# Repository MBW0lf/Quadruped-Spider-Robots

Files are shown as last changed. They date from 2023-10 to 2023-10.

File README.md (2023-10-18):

# Quadruped-Spider-Robots

<!-- TABLE OF CONTENTS -->
<details>
  <summary>Table of Contents</summary>
  <ol>
    <li><a href="#about-the-project">About The Project</a></li>
    <li><a href="#components">Components</a></li>
    <li><a href="#results">Results</a></li>
    <li><a href="#contact">Contact</a></li>
  </ol>
</details>

<!-- ABOUT THE PROJECT -->
# About The Project

In this project, we initially designed the robot model, manufactured the robot components using a 3D printer, and assembled them. Subsequently, we programmed the robot's movements. Finally, employing image processing, we detected obstacles and reached the destination using existing algorithms.

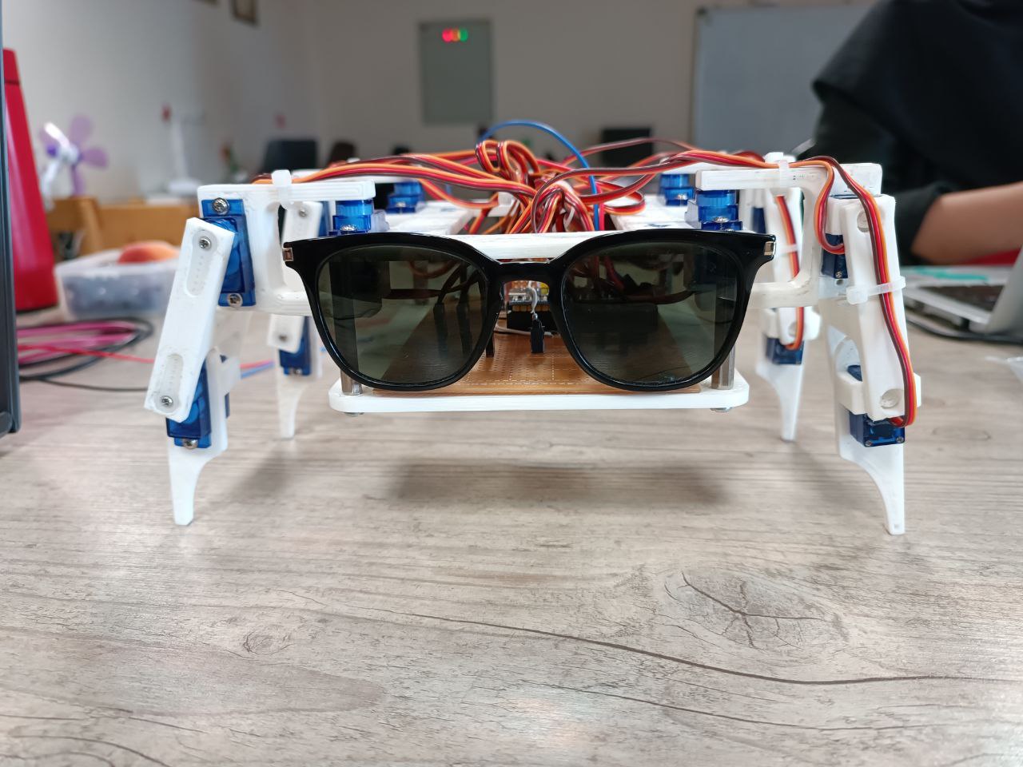
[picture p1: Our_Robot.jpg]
 

<p align="right">(<a href="#top">back to top</a>)</p>

# Components
 * Main proccessor: [STM32F103C8T6 (ARM Cortex-M3)](https://amjadkala.com/product/stm32f103c8t6-board/)
 * Motor: [Servo Motor SG90](https://eshop.eca.ir/%D8%B3%D8%B1%D9%88%D9%88%D9%85%D9%88%D8%AA%D9%88%D8%B1/2551-%D8%B3%D8%B1%D9%88-%D9%85%D9%88%D8%AA%D9%88%D8%B1-t-pro-mini-servo-sg90-9g-servo.htm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)
 * Camera: [ESP32-CAM](https://eshop.eca.ir/%D9%85%D8%A7%DA%98%D9%88%D9%84-%D9%BE%D8%B1%D8%AF%D8%A7%D8%B2%D8%B4-%D8%AA%D8%B5%D9%88%DB%8C%D8%B1-%D9%88-%D8%AF%D9%88%D8%B1%D8%A8%DB%8C%D9%86/1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) 
 * Source Voltage: [HJS-480-0-24](https://bir-robotic.ir/product/%D9%85%D9%86%D8%A8%D8%B9-%D8%AA%D8%BA%D8%B0%DB%8C%D9%87-%D8%B3%D9%88%D8%A6%DB%8C%DA%86%DB%8C%D9%86%DA%AF-24-%D9%88%D9%84%D8%AA-20-%D8%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)
 
<p align="right">(<a href="#top">back to top</a>)</p>

<!-- PARTS -->
# Results

**Robot Without Motors**

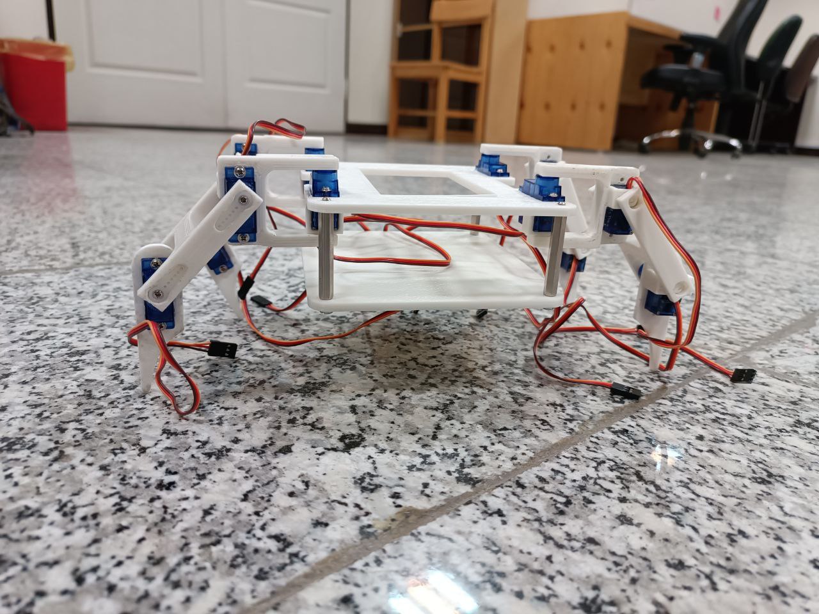
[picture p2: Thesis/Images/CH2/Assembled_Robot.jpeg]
 

**Robot From The Front**

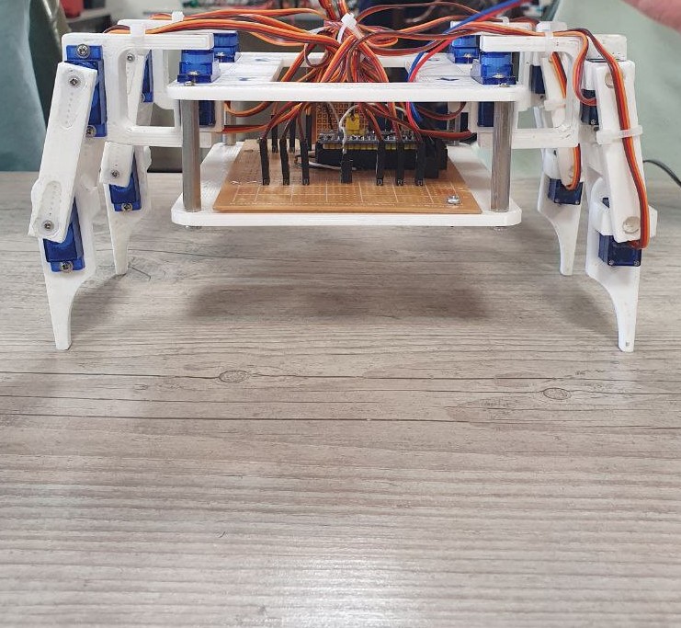
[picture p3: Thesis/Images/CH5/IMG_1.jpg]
 

**Robot From The Top**

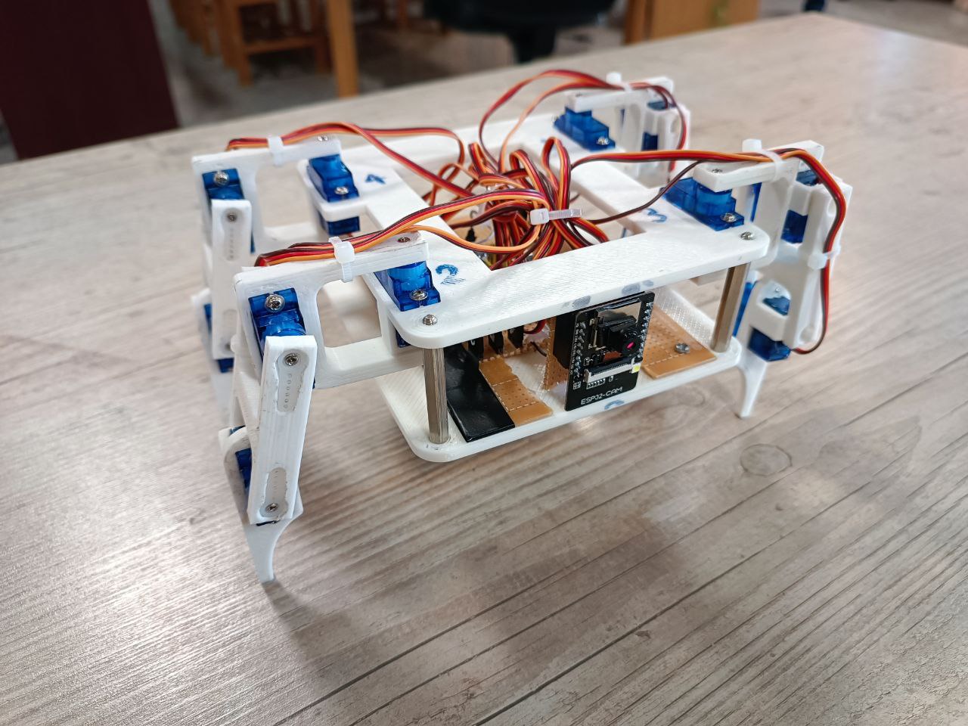
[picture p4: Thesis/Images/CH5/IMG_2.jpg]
 

**Final Verion In SolidWorks**

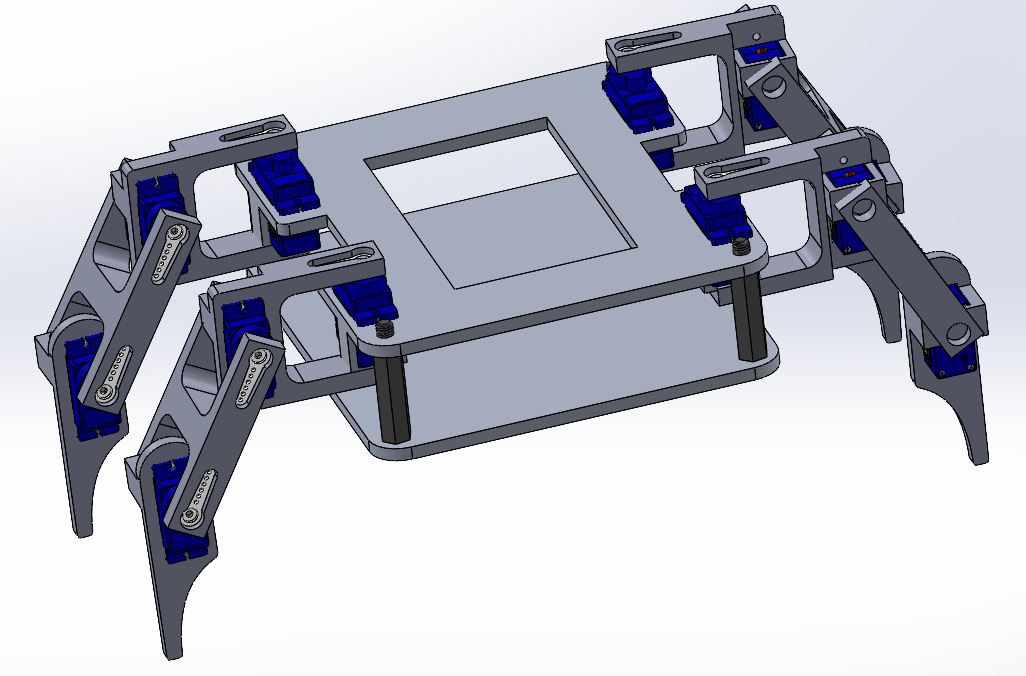
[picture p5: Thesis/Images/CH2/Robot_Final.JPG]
 

<p align="right">(<a href="#top">back to top</a>)</p>

<!-- CONTACT -->
# Contact

Mohammad Barabadi - [@MBW0lf](https://github.com/MBW0lf) - reyneh.100.mb@gmail.com

Sajad Ghadiri - [@Sajad-Ghadiri](https://github.com/Sajad-Ghadiri) - cjanthony.romeo@gmail.com

Project Links: [https://github.com/MBW0lf/Quadruped-Spider-Robots](https://github.com/MBW0lf/Quadruped-Spider-Robots)

<p align="right">(<a href="#top">back to top</a>)</p>

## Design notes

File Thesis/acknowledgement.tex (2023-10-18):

%%%%%%%%%%%%%%%%%%%%%%%%%%%%%%%%%%%%
\newpage\thispagestyle{empty}
% سپاس‌گزاری
\textbf{تقدیر و تشکر}
\\[2cm]

تشکر قلبی و لسانی خود را از استاد عالی قدر جناب دکتر محمد اعظم خسروی که زحمت راهنمایی این پایان نامه را عهده دار گردیدند و در تمامی مراحل انجام رساله از راهنمایی‌های مدبّرانه ایشان استفاده نمودم ابراز می‌دارم و توفیقات روز افزون ایشان را توأم با صحت و سعادت خواستارم.

از جناب دكتر مسعود شفيعي كه زحمت داوري و تصحيح اين پايان نامه را به عهده داشتند كمال سپاس را دارم.

از همگروهي عزيز مهندس سجاد قدیری كه همواره يار و ياوري صبور بود كمال تشكر را دارم.
 
و در پایان از تمامی عزیزانی که در طول انجام این پروژه مرا یاری کرده‌اند کمال تشکر و قدردانی را ابراز می‌نمایم.

% با استفاده از دستور زیر، امضای شما، به طور خودکار، درج می‌شود.
%\signature

%%%%%%%%%%%%%%%%%%%%%%%%%%%%%%%%%%%%%%%%%
%%%%%%%%%%%%%%%%%%%%%%%%%%%%%%%%%کدهای زیر را تغییر ندهید.
\newpage\clearpage

\pagestyle{style2}

\vspace*{-1cm}
\section*{\centering چکیده}
%\addcontentsline{toc}{chapter}{چکیده}
\vspace*{.5cm}
\ffa-abstract
\vspace*{2cm}

{\noindent\large\textbf{واژه‌های کلیدی:}}\par
\vspace*{.5cm}
\fkeywords

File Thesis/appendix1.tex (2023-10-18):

\chapter*{‌پیوست}
\markboth{پیوست}{}
\addcontentsline{toc}{chapter}{پیوست}
کد کامل شامل 1300 خط است که به چندین فایل تقسیم کردیم که ما داخل فایل \lr{Main} تغییرات را ایجاد می‌کنیم و در اینجا توابع و دستورات مهم را آوردیم.

    \begin{figure}[!h]
	\centering
	
	
	\vspace{0.5cm}
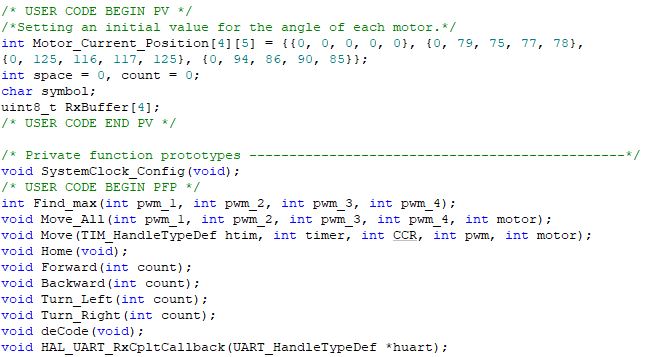
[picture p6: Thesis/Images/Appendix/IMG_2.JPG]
	
	\end{figure}
	
	\begin{figure}[!h]
	\centering
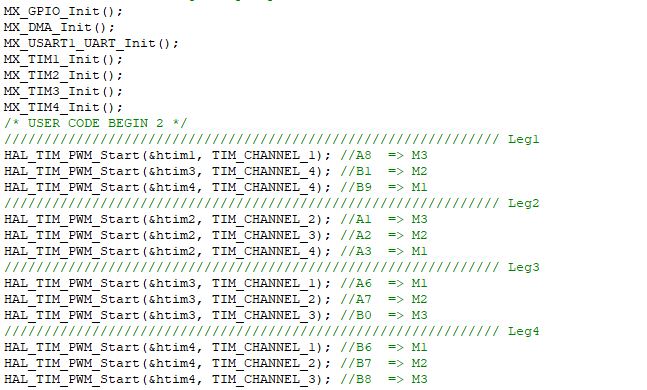
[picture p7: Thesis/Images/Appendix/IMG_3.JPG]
	
		
	\vspace{0.5cm}
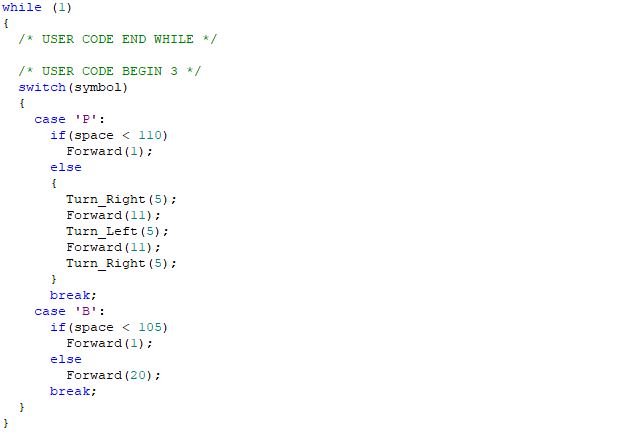
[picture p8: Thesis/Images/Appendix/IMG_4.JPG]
	
	\end{figure}
	
	\begin{figure}[!h]
	\centering
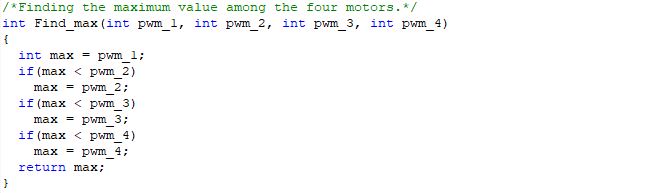
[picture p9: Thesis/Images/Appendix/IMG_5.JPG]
	
		
	\vspace{0.5cm}
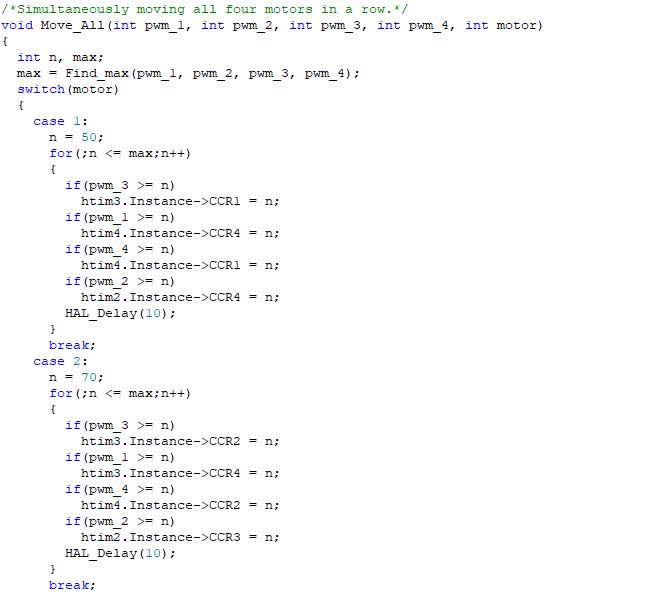
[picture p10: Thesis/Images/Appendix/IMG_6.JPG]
	
	\end{figure}
	
	\begin{figure}[!h]
	\centering
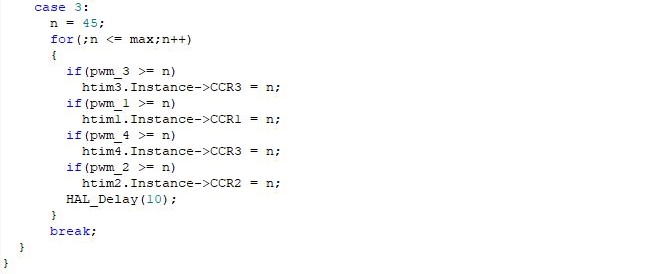
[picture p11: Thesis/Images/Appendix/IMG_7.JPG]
	
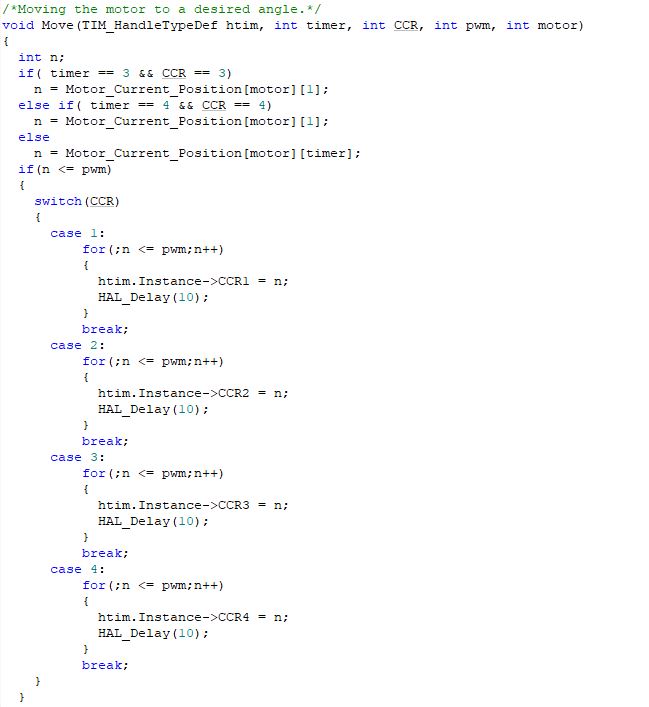
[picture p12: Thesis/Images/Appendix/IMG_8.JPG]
	
	\end{figure}
	
	\begin{figure}[!h]
	\centering
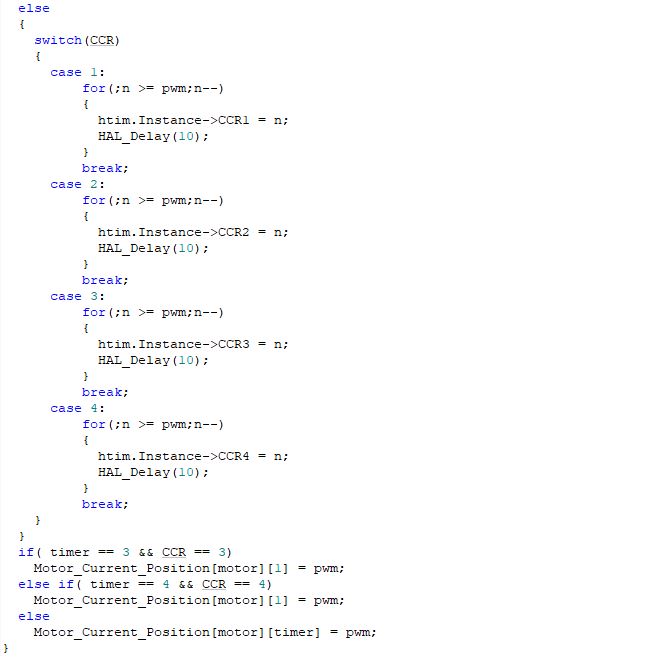
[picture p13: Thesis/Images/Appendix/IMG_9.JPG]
	
			
	\vspace{0.5cm}
	
	\end{figure}
	
	\begin{figure}[!h]
	\centering
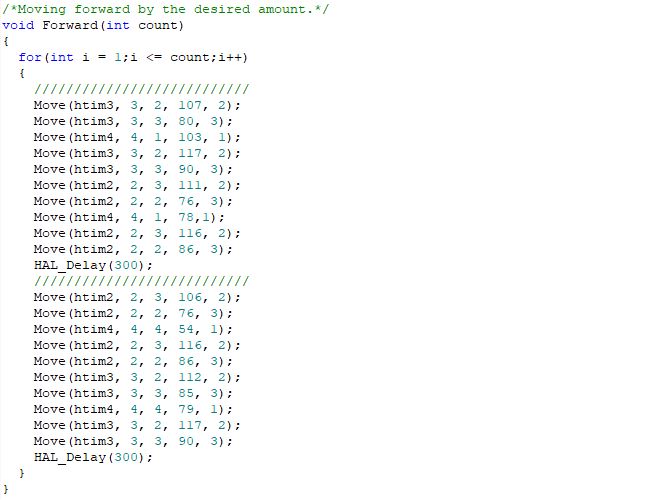
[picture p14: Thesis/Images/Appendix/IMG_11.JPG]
	
		
	\vspace{0.5cm}
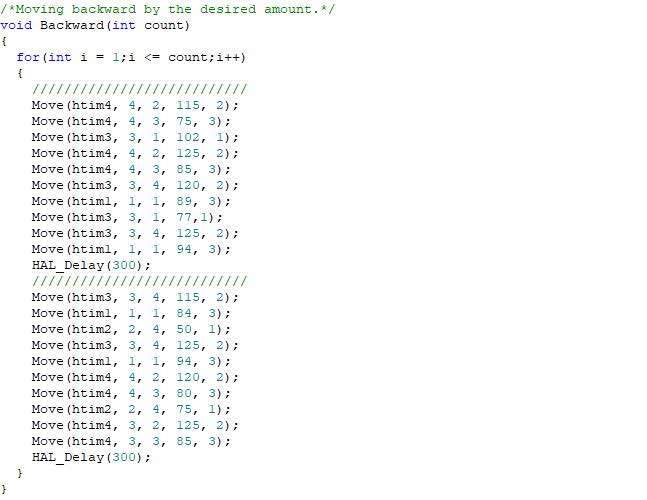
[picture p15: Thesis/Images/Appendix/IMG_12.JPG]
	
	\end{figure}
	
	\begin{figure}[!h]
	\centering
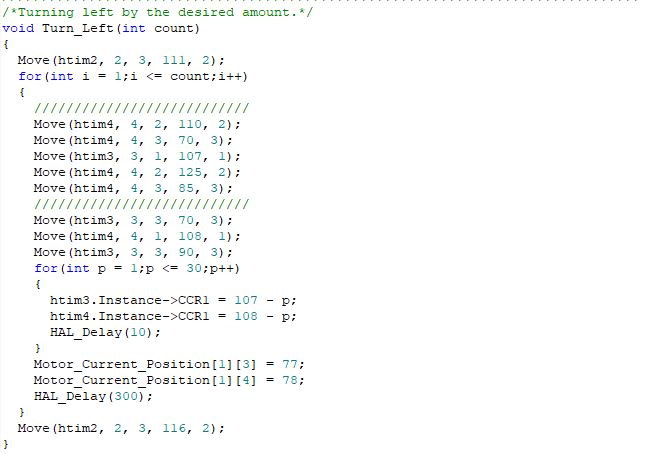
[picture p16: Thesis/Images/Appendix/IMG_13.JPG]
	
	
	\vspace{0.5cm}
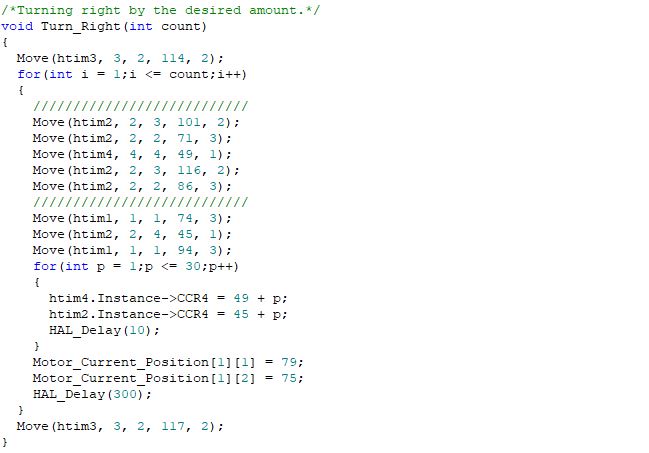
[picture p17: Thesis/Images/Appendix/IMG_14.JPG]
	
	\end{figure}	
	
	\begin{figure}[!h]
	\centering
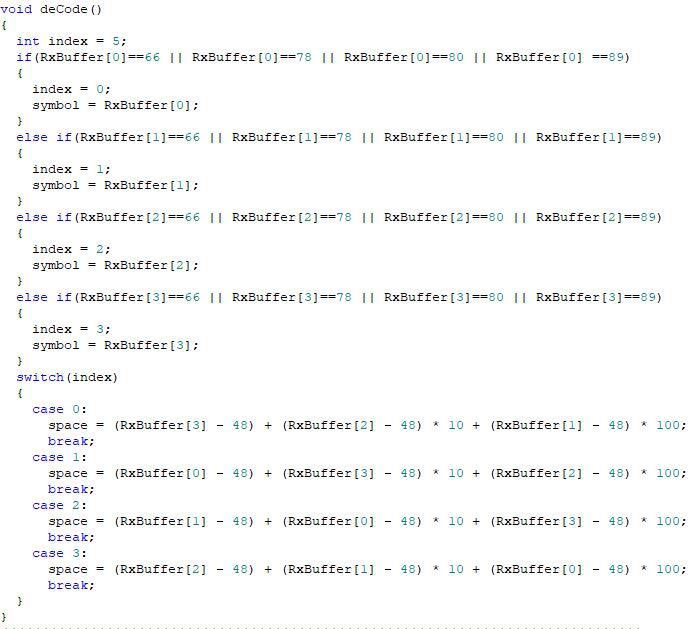
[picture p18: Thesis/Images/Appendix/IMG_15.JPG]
	
	
	\vspace{0.5cm}
	
	\end{figure}

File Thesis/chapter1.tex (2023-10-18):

\chapter{مقدمه}

\section{مقدمه}
با پیشرفت‌های چشمگیر در فناوری و مهندسی در چند دهه اخیر، یک انقلاب قابل توجه در زمینه رباتیک رخ داده است. رباتیک به عنوان یک زمینه چندجانبه و قابل اجرا، شامل تحقیقات و توسعه در طراحی، ساخت، کنترل و بهینه‌سازی ربات‌ها می‌شود. با ترکیب فناوری‌های مختلف از جمله مکانیک، الکترونیک، نرم‌افزار و هوش مصنوعی، ربات‌ها به وجود می‌آیند که قادر به انجام طیف گسترده‌ای از وظایف هستند؛ از فعالیت‌های صنعتی و خدماتی تا کارهای پزشکی، کشاورزی و حتی بررسی فضا.

امروزه از علم رباتیک برای ایجاد دستگاه‌های خودکار به کمک هوش مصنوعی که بتوانند وظایفی مشابه انسان‌ها را با دقت و کارایی بیشتری انجام دهند، استفاده می‌شود. برای رسیدن به این هدف، محققان و مهندسان در زمینه رباتیک تلاش می‌کنند تا مکانیسم‌های پیچیده‌تری برای حرکت، احساس، تصمیم‌گیری و تعامل با محیط ایجاد کنند.

\section[ربات و انواع آن]{ربات و انواع آن\cite{Digiato}}
ربات یک ماشین است (به‌خصوص ماشینی که توسط کامپیوتر قابل برنامه‌نویسی باشد) که می‌تواند مجموعه کارهای پیچیده‌ای را به‌صورت خودکار انجام دهد.ربات‌ها ممکن است توسط یک دستگاه کنترل خارجی، کنترل شوند یا این‌که دستگاه کنترلی در داخل آن‌ها قرار بگیرد. ربات‌ها ممکن است به‌گونه‌ای ساخته شوند که ظاهری شبیه به انسان داشته باشند اما بیشتر ربات‌ها، ماشین‌هایی هستند که برای انجام کاری ساخته می‌شوند و ظاهر آن‌ها اهمیتی ندارد. 

ربات‌ها ممکن است خودران\LTRfootnote{Autonomous} یا نیمه خودران\LTRfootnote{Semi-Autonomous} باشند و انواع مختلفی دارند؛ از قبیل ربات‌های انسان‌نما، مانند ربات
\lr{ASIMO}
 شرکت هوندا و ربات پینگ‌پونگ‌باز شرکت 
\lr{TOSY}
، ربات‌های صنعتی، ربات‌های جراحی پزشکی، ربات‌های کوچک که از هوش جمعی بهره می‌برند، پهباد هایی مانند هواپیمای بدون سرنشین
\lr{Predator MQ-1}
که توسط نیروی هوایی ایالات‌ متحده مورداستفاده قرار می‌گیرد و حتی ربات‌های میکروسکوپی(نانو ربات‌ها)\cite{Digiato}. ربات‌ها ممکن است با تقلید از ظاهر موجودات زنده و یا شبیه‌سازی حرکات آن‌ها، حس هوشمند بودن و یا توانایی فکر کردن را به انسان القا کنند. انتظار می‌رود تا در دهه آتی، اشیا خودران گسترش چشمگیری پیدا کنند. از ارکان اصلی این گسترش می‌توان به ربات‌های خانگی و اتومبیل‌های خودران اشاره کرد.
\newpage
ربات‌ها انواع گوناگونی دارند و هر نوع برای کاربردهای خاصی طراحی شده است. در ادامه به بررسی برخی از انواع مختلف ربات‌ها و ویژگی‌های منحصربه‌فرد آنها می‌پردازیم:

\vspace{0.5cm}
\textbf{1- ربات‌های صنعتی}:
  امروزه پیچیدگی‌های فرایند تولید در صنایع مختلف، افزایش حجم کار و البته رقابتی بودن بازار، منجر به جایگزینی ربات صنعتی با نیروی انسانی شده است. واقعیت این است که در نظر گرفتن حفظ سلامت نیروی کار، جلوگیری از بروز خطا حین فرایند تولید و افزایش سرعت ایجاب می‌کند که از ربات ها به ویژه ربات صنعتی به عنوان بهترین جایگزین برای نیروی انسانی استفاده شود.
  
  ربات صنعتی در واقع یک سیستم اتوماتیک است که برای انجام مراحل مختلف فرآیند تولید محصول در انواع صنایع استفاده می‌شود. اغلب این ربات‌ها به طور کامل قابل برنامه‌ریزی هستند و سرعت و دقت انجام کار را به طور چشم‌گیری افزایش می‌دهند. ربات های صنعتی در ابعاد مختلف تولید می‌شوند؛ از نانو و میکرو گرفته تا ابعاد بزرگتر و کارخانه‌ای، قابلیت اضافه شدن به خط تولید را دارند.
    \begin{figure}[!h]
  	\vspace{0.2cm}
  	\centering
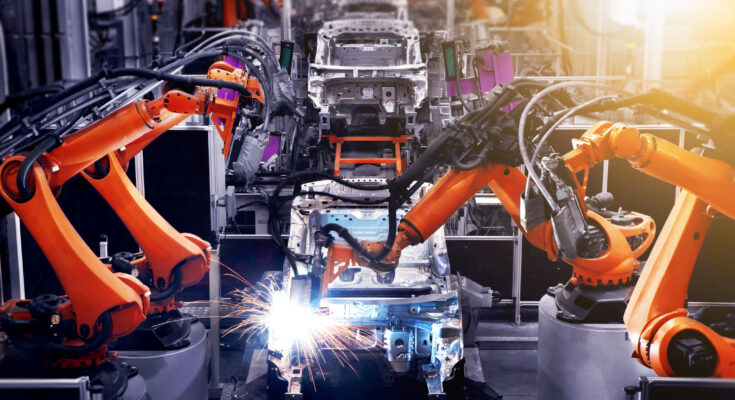
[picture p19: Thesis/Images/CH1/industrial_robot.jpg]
  	
  	\caption{نمونه ربات صنعتی}
  	\label{ربات سنعتی}
    \end{figure}

\textbf{2- ربات‌های خدماتی}:
  ربات‌های خدماتی، نوعی سیستم هوش مصنوعی، به عنوان یک پیشرفت فناوری مهم در سال‌های اخیر ظهور کرده‌اند. این ربات‌ها برای انجام وظایف و عملکردهای متنوع در محیط‌های مختلف طراحی و برنامه‌ریزی شده‌اند تا زندگی انسان‌ها را بهبود بخشند و خدمات گوناگونی را فراهم آورند. برخلاف ربات‌های صنعتی که عمدتاً در کارخانه‌ها عمل می‌کنند، ربات‌های خدماتی برای تعامل مستقیم با انسان‌ها طراحی شده‌اند و در محیط‌های مختلفی نظیر خانه‌ها، مراکز درمانی، بخش هتل‌ها، فضاهای عمومی و غیره عمل می‌کنند.
\newpage
\begin{itemize}
	\item ربات‌های خانگی: این ربات‌ها در کمک به کارهای خانگی نظیر جارو‌کردن، کوتاه کردن چمن و تمیز کردن استفاده می‌شوند.
    \begin{figure}[!h]
	\vspace{0.2cm}
	\centering
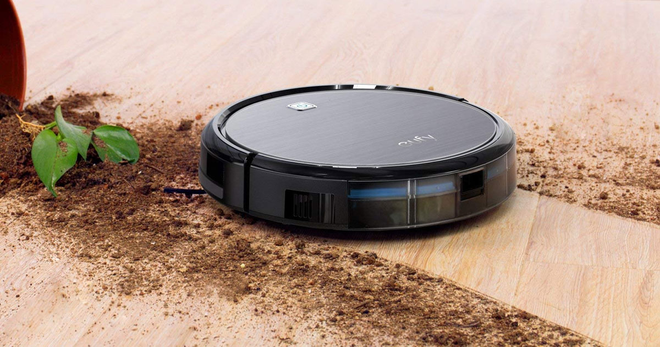
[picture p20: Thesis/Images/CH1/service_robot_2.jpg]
	
	\caption{نمونه‌ای از ربات خانگی}
	\label{ربات خانگی}
	\end{figure}
	
	\item ربات‌های پزشکی: در محیط‌های درمانی برای انجام عملیات‌های جراحی، مراقبت از بیماران و بازسازی استفاده می‌شوند.
    \begin{figure}[!h]
	\vspace{0.2cm}
	\centering
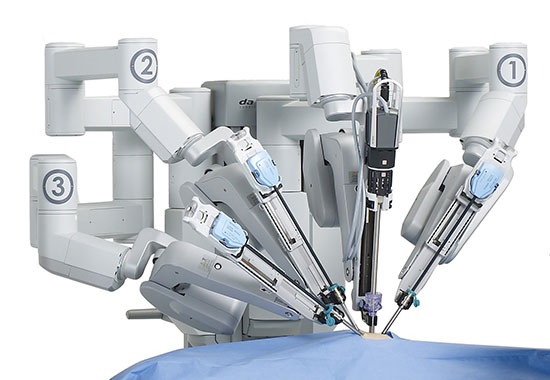
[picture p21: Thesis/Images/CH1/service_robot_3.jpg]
	
	\caption{ربات جراح}
	\label{ربات جراح}
	\end{figure}

	\item ربات‌های سرگرمی: برای اهداف سرگرمی طراحی شده‌اند، از اسباب‌بازی‌ها و همراهان رباتی تا کاربردهای سرگرمی دیگر.
	
    \begin{figure}[!h]
	\vspace{0.2cm}
	\centering
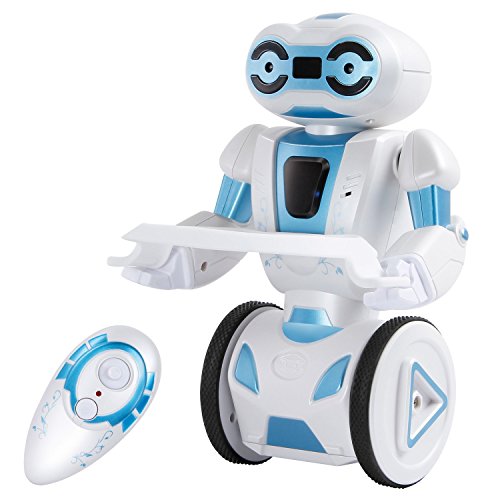
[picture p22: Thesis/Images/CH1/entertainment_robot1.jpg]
	
	\caption{یک نمونه ربات سرگرمی}
	\label{ربات سرگرمی}
	\end{figure}

\end{itemize}	
 
\textbf{3- وسایل خودران}:
  ربات‌های خودران می‌توانند وظایف خود را به‌صورت کاملاً خودکار و بدون نیاز به نظارت و کنترل انسان انجام دهند. این ربات‌ها معمولاً برای فعالیت در محیط‌های باز که فعالیت کردن در آن‌ها نیازی به نظارت انسان ندارد، طراحی شده‌اند. چنین ربات‌هایی طراحی منحصربه‌فردی دارند؛ زیرا با برخورداری از سنسورهای مختلف می‌توانند محیط اطراف خود را به‌خوبی درک کنند و سپس با بهره‌مندی با آن دسته از تجهیزات خود که برای تصمیم‌گیری به ربات کمک می‌کنند (معمولاً کامپیوترهای خاصی این کار را انجام می‌دهند)، بر اساس داده‌های در اختیار خود و همچنین مأموریتی که به آن‌ها محول شده است، تصمیم مناسب را برای انجام کار بعدی به بهترین شکل ممکن می‌گیرند.
    \begin{figure}[!h]
	\vspace{0.2cm}
	\centering
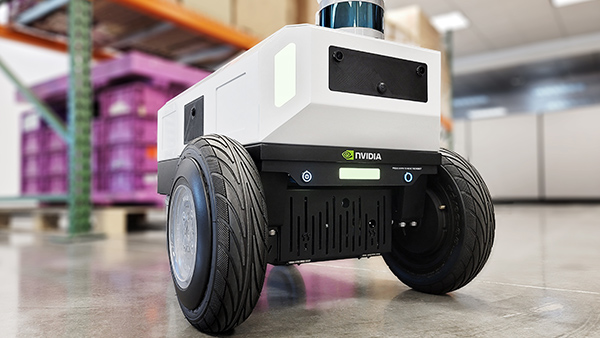
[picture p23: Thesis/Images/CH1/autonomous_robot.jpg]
	
‌	\caption{نمونه‌ای از ربات خودران}
	\label{ربات خودران}
	\end{figure}
	
\textbf{4- ربات‌های نظامی و دفاعی}:
  این ربات‌ها برای کاربردهای نظامی طراحی شده‌اند، از جمله نظارت، انجام مأموریت‌های مهم و مبارزه از راه دور. آنها در محیط‌های چالشی عمل می‌کنند تا خطرات برای سربازان انسانی را کمینه کنند.
  سلاح‌ها و تجهیزات نظامی رباتیک مجهز به هوش مصنوعی نیز می‌توانند یک برگ برنده طلایی برای پیروزی در جنگ‌ها باشند؛ به‌عنوان ‌مثال سامانه پیشرفته نظامی مدولار مارس
\lr{MAARS}
\unskip\LTRfootnote{Modular Advanced Armed Robotic System} 
با ظاهری شبیه به تانک مجهز به قابلیت پرتاب گاز اشک‌آور و انتشار اشعه لیزر جهت سردرگم کردن دشمن و همچنین یک نارنجک‌انداز برای زمین‌گیر کردن دشمن است\cite{Digiato}.
    \begin{figure}[!h]
	\vspace{0.2cm}
	\centering
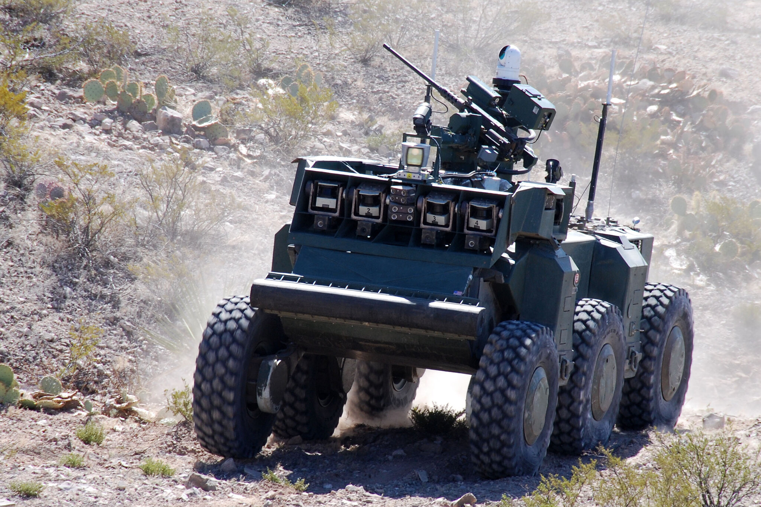
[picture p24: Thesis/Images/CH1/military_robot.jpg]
	
	‌\caption{ربات نظامی}
	\label{ربات نظامی}
	\end{figure}
\newpage
\textbf{5- ربات‌های آموزشی}:	
  ربات‌های آموزشی برای آموزش برنامه‌نویسی، مهندسی و مهارت‌های حل مسئله به دانش‌آموزان استفاده می‌شوند. آنها از کیت‌های ساده برای مبتدیان تا پلتفرم‌های پیچیده‌تر برای دانشجویان پیشرفته متفاوتی دارند.
    \begin{figure}[!h]
	\vspace{0.2cm}
	\centering
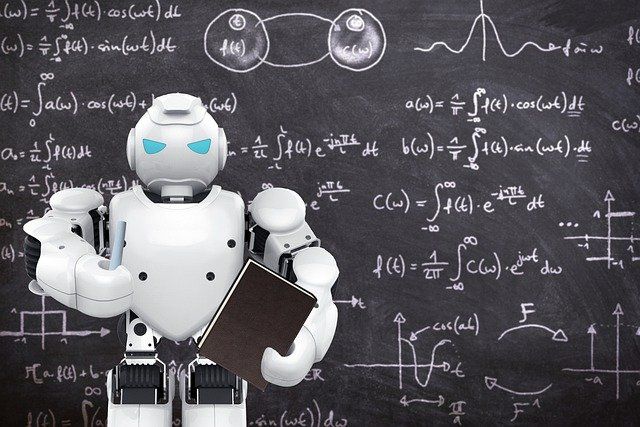
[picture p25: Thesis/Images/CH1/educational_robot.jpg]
	
	‌\caption{ربات آموزگار}
	\end{figure}
	
\textbf{6- ربات‌های کشاورزی}: 
  انجام برخی از امور کشاورزی توسط کشاورزان وقت زیادی از آن‌ها می‌گیرد. چنانچه آن‌ها برای انجام چنین کارهایی از ربات‌ها کمک بگیرند، شاهد نتیجه بهتری خواهند بود. این امور شامل فعالیت‌های مرتبط با کاشت و بذرپاشی، کنترل علف‌های هرز، برداشت و سایر فعالیت‌های مشابه می‌شود.
  
  برداشت محصولات کشاورزی با کمک ربات‌ها در مقایسه با انجام این کار به‌صورت سنتی و توسط کشاورزان، نیز نتیجه بهتری دارد. برای انجام این کار نیز ربات‌های مخصوصی طراحی شده‌اند. برخی از این ربات‌ها دارای بازوهای مخصوص برای برداشت و چیدن میوه‌های تابستانی حساس با بافت نرم مثل انگور، انواع توت‌ها و... جهت جلوگیری از آسیب دیدن آن‌ها هستند.
    \begin{figure}[!h]
	\vspace{0.2cm}
	\centering
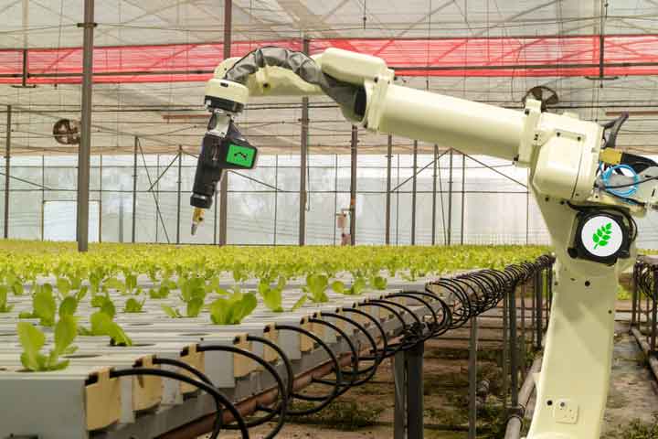
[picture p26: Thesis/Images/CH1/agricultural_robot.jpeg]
	
	‌\caption{یک نمونه ربات کشاورز}
	\label{ربات کشاورزی}
	\end{figure}
	
\textbf{7- ربات‌های پزشکی}: 
  ربات‌ها در این حوزه می‌توانند به‌عنوان دستیار جراح استفاده شوند. آن‌ها می‌توانند در جراحی قسمت‌های حساس بدن مثل گردن و ستون فقرات که کوچک‌ترین اشتباه در جراحی آن‌ها آسیب‌های جبران‌ناپذیری را به بار می‌آورد، کمک دست جراحان شوند و دقت جراحی را افزایش دهند. حتی برخی از جراحی‌ها به‌قدری دقت بالایی می‌طلبند که انسان قادر به انجام آن‌ها نیست و برای انجام آن‌ها ناگزیر باید از ربات استفاده کند؛ به‌عنوان مثال شرکت نورالینک
\unskip\LTRfootnote{Neuralink}
 قصد دارد یک تراشه مغزی برای برقراری ارتباط بین مغز انسان و دستگاه‌های مختلف جهت کنترل ذهن‌ها و همچنین درمان اختلالات و بیماری‌های مغزی عرضه کند و جراحی لازم برای قرار دادن این تراشه مغزی به‌قدری دقت زیادی می‌طلبد که انسان قادر به انجام آن نیست و نورالینک یک ربات برای این جراحی نیز طراحی کرده‌است.
    \begin{figure}[!h]
	\vspace{0.2cm}
	\centering
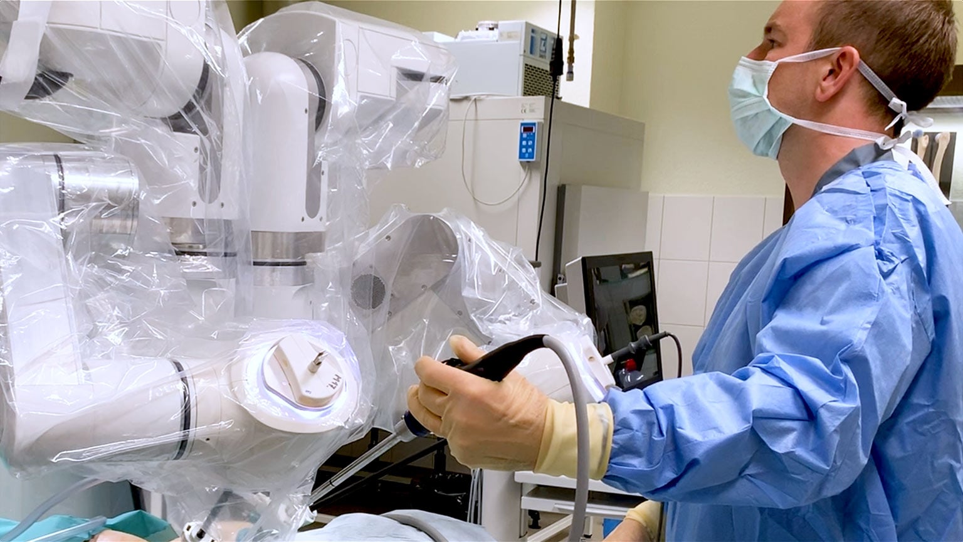
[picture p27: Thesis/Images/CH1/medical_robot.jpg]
	
	‌\caption{یک نمونه ربات پزشکی}
	\label{ربات پزشکی}
	\end{figure}
	
\textbf{8- ربات‌های انسان‌نما}:  
  ربات‌های انسان‌نما ظاهری شبیه به انسان دارند کارهای و رفتارهای او را تقلید می‌کنند. این ربات‌ها قادر به انجام فعالیت‌های شبیه به فعالیت‌های انسانی هستند که از میان آن‌ها می‌توان به دویدن، پریدن و حمل اشیا اشاره کرد. ظاهر برخی از ربات‌های انسان‌نما کاملاً شبیه انسان‌های واقعی است و اگر به‌صورت گذرا به آن‌ها نگاه کنیم یا از دور آن‌ها را ببینیم، اصلاً متوجه این موضوع نمی‌شویم.
    \begin{figure}[!h]
  	\vspace{0.2cm}
  	\centering
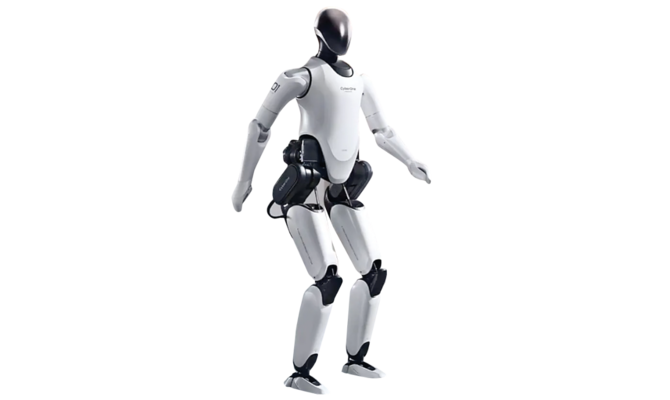
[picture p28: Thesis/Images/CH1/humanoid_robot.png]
  	
  	‌\caption{ربات انسان‌نما}
  	\label{ربات انسان‌نما}
    \end{figure}
    
\section{ربات چهارپا}
در دنیای رباتیک، انواع مختلفی از ربات‌ها وجود دارند که با توجه به تنوع ویژگی‌هایشان، برای انجام وظایف گوناگون طراحی و ساخته می‌شوند. یکی از این انواع ربات‌ها که در سال‌های اخیر توجه زیادی به خود جلب کرده است، ربات‌های چهارپا (ربات‌های با چهار پا) هستند. این ربات‌ها با تقلید از حرکات و رفتار حیوانات دارای چهار پا مانند سگ، گربه و حتی عنکبوت‌ها طراحی می‌شوند.
\subsection{ویژگی‌های ربات چهارپا}
تمایل انسان به به‌كارگیري ظرفیت‌هاي طبیعت، بدست آوردن فهم بهتر از راه رفتن و حرکات چابک جانوران طبیعی، و الگوبرداري و شبیه‌سازي ماشینی رفتار حیوانات از جمله دلایل رویكرد به ربات‌هاي پادار است. در میان ربات‌هاي پادار، ربات‌هاي چهارپا به علت پایداري مناسب‌تر نسبت به ربات‌هاي دو پا و نیز تعداد پاهاي کمتر نسبت به ربات‌هاي شش پا، پیچیدگی کمتر را در طراحی داشته و مانورهاي مختلف ممكن را که از ربات‌هاي پادار انتظار می‌رود دارا است.

ربات‌هاي چهارپا نسبت به ربات‌هاي چرخ‌دار و شنی‌دار داراي مزایایی هستند که استفاده از آنها را در برخی زمینه‌ها توجیه می‌کند. از جمله این قابلیت‌ها می‌توان از سازگاري با محیط‌هاي ناهموار، جابجایی کارآمد، تعلیق پویاو فعال با زاویه دادن به بندگاه‌ها
\unskip\LTRfootnote{Joints}
،عبور از موانع، مصرف یكسان انرژي در محیط‌هاي هموار و ناهموار، امكان کاهش سر خوردگی با تماس عمودي با زمین نام برد.

با وجود مزایاي ذکر شده، ربات‌هاي پادار راه‌حل کامل مسئله حرکت نیست و مشكلات آنها باعث شده تا به‌كارگیري آنها در صنایع و بخش‌هاي خدماتی با کندي صورت گیرد. از جمله این مشكلات پیچیدگی، توان مصرفی بالا در مقایسه با ربات‌هاي چرخ‌دار در محیط‌هاي هموار، و سرعت کم آنها است.

\subsection{موارد کاربرد ربات‌های چهارپا}
موارد کاربرد ربات‌هاي چهارپا به مزیت‌هاي آنان نسبت به ربات‌هاي چرخ‌دار باز می‌گردد که شامل کمک به جمع‌آوري اطلاعات در امداد و نجات شهري به هنگام زلزله، آتش‌سوزي، و یا حوادث تروریستی و در جاهایی که حضور پرسنل انسانی داراي ریسک می‌باشد با امكان بالا رفتن و عبور از سطوح ناهموار، حمل بار از نقاط صعب العبور با کنترل از راه دور، اکتشافات سطحی و جستجو در کف دریاها، سطوح کرات
دیگر، قابلیت استفاده در محیط‌هاي پرمانع مانند محیط‌هاي جنگلی،کمک به افراد معلول در حرکت در محیط‌هاي ناهموار و نیز به عنوان ربات‌هاي توان‌بخشی می‌باشد\cite{Quadruped}.
\newpage
\subsection{نمونه‌های پیشین}
\begin{itemize}
\item  
\textbf{ربات آیبو}\unskip\LTRfootnote{AIBO}:
آیبو یک ربات کوچک چهارپا به شكل سگ است که در شرکت سونی
ساخته شده است. پروژه آیبو از سال 1990 شروع شده و مدل‌هاي
مختلفی از آن ساخته شد. مدلی از این ربات که در شکل
\ref{ربات آیبو}
مشاهده می‌شود در سال 2003 به منظور مسابقات جهانی ارائه گردید. این ربات به ازاي هرپا داراي سه درجه آزادي است و با هدف سرگرمی ساخته شده است که در طراحی این ربات از سرو موتورهاي جدیدي با گشتاور بالا استفاده شده است. این ربات براي یک ساعت حداقل بدون شارژ کردن مجدد می‌تواند کار کند\cite{AIBO}.
    \begin{figure}[!h]
	\vspace{0.2cm}
	\centering
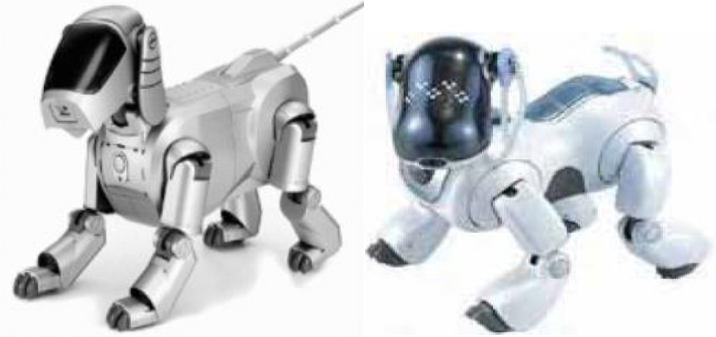
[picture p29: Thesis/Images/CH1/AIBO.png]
	
	‌\caption[ربات چهارپای آیبو]{ربات چهارپای آیبو\cite{AIBO}}
	\label{ربات آیبو}
	\end{figure}
	
\item	
\textbf{ربات جی-داگ}\LTRfootnote{G-Dog}:
کمپانی رباتیكی ژاپنی
\lr{HPI} 
 در حال تبلیغ جدیدترین محصول
تجاري خود به نام جی-داگ 3 با قیمتی معادل 550 یورو می‌باشد که در شكل
\ref{ربات جی‌داگ}
مشاهده می‌شود. واحد پردازشگر این ربات از نوع 
\lr{11-RPU}
است و ارتفاع ربات به 19 سانتیمتر می‌رسد. از طریق درگاه
\lr{RS232}
می‌توان اتصال میان ربات و کامپوتر برقرار و حرکات آن را برنامه‌ریزي نمود. این ربات داراي نه سرو موتور است که در هر پا دو موتور قرار گرفته‌است که در کل نه درجه آزادي به این ربات می‌دهد. قابلیت اضافه‌کردن موتورهاي اضافه نیز به این ربات وجود دارد\cite{G-Dog}.
    \begin{figure}[!h]	
	\vspace{0.2cm}
	\centering
	
	‌\caption[ربات جی‌داگ]{ربات جی‌داگ\cite{G-Dog}}
	\label{ربات جی‌داگ}
	\end{figure}

\newpage
\item
\textbf{سگ کوچک}\unskip\LTRfootnote{Little Dog}:
سگ کوچک یک ربات چهارپاست که به منظور انجام تحقیقات در خصوص یادگیري گام‌برداري
\unskip\LTRfootnote{Locomotion}
به خصوص در زمین‌هاي ناهموار توسط شرکت بوستون داینمیكس در سال 2006 میلادي با حمایت
\lr{DARPA}\unskip\LTRfootnote{Defense Advanced Research Projects Agency}
ساخته شده\cite{Little-Dog-1} که در شكل
\ref{ربات سگ کوچک}
نمایش داده شده است. ربات سگ کوچک داراي  30 سانتیمتر طول، 18 سانتیمتر عرض، و 26 سانتیمتر ارتفاع است و وزن آن تقریباً برابر با 2/5 کیلوگرم است\cite{Little-Dog-2}.
این ربات داراي سه موتور الكتریكی براي کنترل هر پا می‌باشد که
مجموعا 12 درجه آزادي را به آن می‌دهند. در طراحی این ربات سعی
شده که موتورها تا حد امكان در نزدیكی بدن قرار گرفته تا اندازه پاها کوچک بمانند. همچنین از یک فنر براي گرفتن ارتعاشات سطوح در
پایین هر پا استفاده شده است. هر کدام از راه‌اندازنده موتورها با فرکانس 100هرتز با یک کنترلگر
\lr{PD} 
زاویه و یا گشتاور توسط یک کامپیوتر تحت سیستم عامل
\lr{Linux}
کنترل میگردد. سگ کوچک داراي چهار حسگر تماس در پاها و یک حسگر مجاورتی
\unskip\LTRfootnote{Proximity}
در سر و حسگر زاویه در تمامی بندگاه ها، و یک واحد اندازه‌گیري اینرسی
\lr{(IMU)}\unskip\LTRfootnote{Inertial Measuring Unit}
براي تنظیم موقعیت بدنه و شتاب آن است. سگ کوچک داراي یک باتري قابل شارژ است که انرژي آن را براي 30 دقیقه حرکت مستمر تأمین می‌نماید\cite{Little-Dog-2}.
    \begin{figure}[!h]
	\vspace{0.2cm}
	\centering
	
	‌\caption[ربات سگ کوچک]{ربات سگ کوچک\cite{Little-Dog-1}}
	\label{ربات سگ کوچک}
	\end{figure}

\newpage
\item 
\textbf{سگ بزرگ}\unskip\LTRfootnote{Big Dog}:
ربات سگ بزرگ محصول شرکت بوستون داینامیكس
\unskip\LTRfootnote{Boston Dynamics}
است و داراي قابلیت‌هاي منحصر به فردي در مانور دادن در محیط‌هاي طبیعی و خشن می‌باشد. این ربات قادر است بارهاي نسبتا سنگین تا حدود دو برابر وزن خود را در زمین‌هاي شیب دار، برفی و یخ زده حمل نماید. ربات سگ بزرگ قادر به دویدن می‌باشد و در حال حاضر به عنوان پیشرفته‌ترین ربات چهارپا در جهان شناخته می‌شود. ساخت این ربات تحت حمایت 30 میلیون دلاريِ آژانس طرح‌هاي پژوهشی پیشرفته دفاعی
\lr{DARPA} 
انجام گردیده است و در افغانستان نیز عملیات آزمایشی انجام داده است. 

ربات سگ بزرگ 109 کیلوگرم وزن دارد و 1 متر ارتفاع، 1/1 متر طول و 0/3 متر عرض دارد. این ربات قادر است 50 کیلوگرم بار را حمل نماید و نیز قادر است بدون بار مسافت 10 کیلومتر را در 2/5 ساعت بدون سوخت‌گیري طی نماید. این چهارپا قادر به پرش تا 1/1 متر نیز می‌باشد.
همان‌گونه که در شكل 1-14 مشاهده می‌شود، هر پاي این ربات داراي 4 درجه آزادي فعال (دو عدد در لگن، و یكی در زانو و یكی در مچ) و یک درجه آزادي غیر فعال (در فنر مچ پا) است. نیروي محرکه آن توسط یک موتور بنزینی تک سیلندر 15 اسب بخار و سیستم هیدرولیک با فشار
\lr{psi} 3000 
 تأمین می‌شود. هر پا توسط چهار شیر سرو الكتروهیدرولیک دو مرحله‌اي کنترل می‌گردد\cite{Big-Dog}.
    \begin{figure}[!h]
	\vspace{0.2cm}
	\centering
	
	‌\caption[ربات سگ بزرگ]{ربات سگ بزرگ\cite{Big-Dog}}
	\label{ربات سگ بزرگ}
	\end{figure}

\newpage
سگ بزرگ داري حسگرهاي متعددي است که شامل: 16 پتانسیومتر خطی براي اندازه‌گیري تغییر زوایاي بندگاه‌هاي زانو، لگن، و مچ پا، 16 عدد حسگر بار 
\unskip\LTRfootnote{Load cell}
براي پاها، 16 عدد حسگر جریان براي پایش جریان شیرهاي سرو، 3 عدد دوربین براي بینایی سه بعدي، یک عدد رادار لیزري (لیدار)
\unskip\LTRfootnote{Lidar}
،یک عدد ژایروسکوپ 
\unskip\LTRfootnote{Gyroscope}
که تغییرات سه زاویه و شتاب خطی سه محور را می‌دهد، دو عدد حسگر ولتاژ باتري می‌باشد. شكل
\ref{حسگر ربات سگ بزرگ}
محل قرار گیري حسگرها را در سگ بزرگ نشان می‌دهد.
    \begin{figure}[!h]
	\vspace{0.2cm}
	\centering
	
	‌\caption{حسگرهاي ربات سگ بزرگ و محل قرارگیري آنها}
	\label{حسگر ربات سگ بزرگ}
	\end{figure}

کامپیوتر روي ربات به‌صورت سفارشی تهیه شده است و داراي پردازشگر پنتیوم با سیستم عامل بلادرنگ
\lr{QNX}
 می‌باشد. کد برنامه به زبان
\lr{C++}
 نوشته شده‌است که اطلاعات حسگرها را دریافت و کنترل لازم به راه‌اندازها را اعمال می‌کند و نیز ارتباط با کاربر را نیز فراهم می‌نماید. معماري نرم افزار ربات سگ بزرگ در شكل
\ref{معماری سگ بزرگ}
نمایش داده شده است.
    \begin{figure}[!h]
 	\vspace{0.2cm}
 	\centering
 	
 	‌\caption{معماري نرم‌افزار ربات سگ بزرگ}
 	\label{معماری سگ بزرگ}
 	\end{figure}
 
فرکانس نمونه‌برداري براي اطلاعات مربوط به مسیریابی 2 هرتز، فاصله‌یابی و تشخیص موانع 10 هرتز، تخمین موقعیّت، کنترل و ثبت داده 200 هرتز، محرّک‌ها و راه‌اندازها یک کیلوهرتز می‌باشد. همچنین جلیقه‌اي براي کاربر ربات طراحی گردیده است که با تجهیزات نصب شده بر روي آن کاربر می‌تواند از طریق یک ارتباط رادیویی بی‌سیم 900 مگاهرتز اطلاعات دریافت شده توسط ربات را پایش کرده، و از طریق یک اهرم کنترل، حرکت ربات را کنترل کند.

نمونه پیشرفته تر ربات سگ بزرگ به‌ نام سامانه پشتیبان گروهان
\lr{(LS3)}
\unskip\LTRfootnote{Legged Squad Support System}
 یا سگ آلفا و نیز گربه وحشی
\unskip\LTRfootnote{WildCat}
 می‌باشد که اخیراً توسط همین شرکت و تحت حمایت وزارت دفاع آمریكا ساخته شده است که در شكل
\ref{ربات پشتیبان گروه}
و
\ref{گربه وحشی}
قابل مشاهده‌اند\cite{LS3}\cite{Wild-Cat}. این ربات‌ها بیشتر جنبه نمایشی نظامی داشته و هنوز اطلاعات مستندي در مورد آنها در مقالات علمی موجود نیست. گربه وحشی نمونه پیشرفته تر ربات یوزپلنگ
\lr{MIT}
است و هم اکنون مراحل آزمون و اصلاحات خود را طی می‌کند و قرار است تا سرعت   50 کیلومتر در ساعت بدود.
    \begin{figure}[!h]
	\vspace{0.2cm}
	\centering
	
	‌\caption[دو تصویر از ربات سامانه پشتیبان گروه]{دو تصویر از ربات سامانه پشتیبان گروه\cite{LS3}}
	\label{ربات پشتیبان گروه}
	\end{figure}

    \begin{figure}[!h]
	\centering
	
	‌\caption[گربه وحشی]{گربه وحشی\cite{Wild-Cat}}
	\label{گربه وحشی}
	\end{figure}
	
\newpage	
\item
\textbf{چهارپاي پیرو}:
ربات پیرو
\unskip\LTRfootnote{PQ1-PIRO}
که به طول 50 سانتیمتر می‌باشد، محصول انستیتو کره‌اي پوهانگ 
\unskip\LTRfootnote{Pohang Institute of Intelligent Robotics}
است. ربات چهارپاي پیرو براي انجام عملیاتی نظیر جستجو، کشف و حمل بار در شرایط طبیعی در نظر گرفته شده است (شكل
\ref{ربات پیرو}).
از آنجا که این ربات شباهت زیادي به ربات سگ بزرگ دارد، بسیاري آن را نمونه کره‌اي سگ بزرگ قلمداد کرده و این امر را نشانه علاقه کره به رقابت در عرصه رباتیک در تراز نخست می‌دانند. این ربات داراي سه درجه آزادي در هر پا می‌باشد\cite{Piro}.
    \begin{figure}[!h]
	\centering
	
	\caption[ربات چهارپاي پیرو]{ربات چهارپاي پیرو\cite{Piro}}
	\label{ربات پیرو}
	\end{figure}
	
\item
\textbf{ربات‌هاي آیدین}:
ربات آیدین 1و2و3 
\lr{(AiDIN)}\unskip\LTRfootnote{Artificial Digitigrade for Natural Environment}
ساخت آزمایشگاه رباتیک هوشمند وسیستم‌هاي مكاترونیک
\unskip\LTRfootnote{Intelligent Robotics and Mechatronic Systems Laboratory}
درکره شمالی در سال‌هاي 2007، 2008 و 2013 می‌باشد\cite{Aidin-I-2}\cite{Aidin-III-1}\cite{Aidin-III-2}\cite{Aidin-I-1}. شكل
\ref{ربات آیدین}
نمایی از این دو نسل ربات را نشان می‌دهد. این ربات داراي 10 درجه آزادي فعال و 4 درجه آزادي غیر فعال است. همانطور که در شكل مشاهده می‌شود، پاهاي جلو هرکدام داراي  3 درجه آزادي فعال و یک غیر فعال به صورت فنر و پاهاي عقب داراي 2 درجه آزادي فعال و یک غیر فعال به صورت فنر می‌باشد. پاهاي ربات آیدین2 داراي وزن کمتر و نسبت ساق به ران آن مناسب‌تر انتخاب شده است و نیز مكان مرکز ثقل پاها براي پایداري بهتر اصلاح گردیده است.
    \begin{figure}[!h]
	\centering
	
	\caption[نماي ربات آیدین ( 1راست) و آیدین ( 2چپ)]{نماي ربات آیدین ( 1راست) و آیدین ( 2چپ)\cite{Aidin-I-1}}
	\label{ربات آیدین}
	\end{figure}	

\newpage
هر بندگاه فعّال توسط یک موتور جریان ثابت 20 وات با جعبه با نسبت دور  53:1 تحریک می‌گردد. ربات آیدین داراي دو کنترل‌گر درونی
\unskip\LTRfootnote{Embeded Controller}
اصلی است که به‌صورت کامپیوترهاي تک بُرد پنتیم 3 با فرکانس 800 مگاهرتز با دیسک فلش و کنترل‌گر
\lr{CAN}
\unskip\LTRfootnote{Controller Area Network}
تحت سیستم عامل بلادرنگ
\lr{RTLinux} 
می‌باشد. کامپیوتر تک بورد دیگر که پنتیوم 1/1 گیگاهرتز و داراي شبكه بیسیم است، وظیفه پردازش صدا و تصویر را دارد. انرژي ربات توست یک سیم برق 220 ولت تأمین می‌گردد ولی تمام تبادل اطلاعات ربات با کاربر از طریق شبكه بی‌سیم انجام می‌پذیرد. این ربات همچنین داراي 10 کنترل‌گر کوچک از نوع
\lr{MicroChip PCI 18f458}
می‌باشد که هرکدام به‌طور محلّی یكی از درجات آزادي را کنترل می‌کند.

\item
\textbf{چهارپای هانما}:
چهارپاي هانما
\unskip\LTRfootnote{Hanma}
در سال 2010 در پژوهشكده رباتیک دانشگاه شاندانگ
\lr{(SUCRO)}
\unskip\LTRfootnote{Shandong University Center for Robotics}
چین ساخته شده که داراي 12 درجه آزادي و 50 کیلوگرم وزن بود که البته برق آن از خارج از ربات تأمین می‌گردد\cite{Hanma}. ارتفاع ربات در حالت اولیه 67 سانتی‌متر و طول و عرض آن به ترتیب  100و 40 سانتی‌متر است. براي حرکت بندگاه‌هاي ربات از محرک‌هاي هیدرولیكی استفاده شده است و قادر است 80 کیلوگرم بار را با سرعت  40 سانتی‌متر بر ثانیه منتقل نماید. شكل
\ref{ربات هانما}
دو نما از این ربات چهارپا را نشان می‌دهد.
    \begin{figure}[!h]
	\centering
	
	\caption[ربات چهارپاي هانما]{ربات چهارپاي هانما\cite{Hanma}}
	\label{ربات هانما}
	\end{figure}

\newpage	
\item
\textbf{چهارپاي هایكیو}:
ربات‌ هایكیو
\unskip\LTRfootnote{HyQ}
ساخت انستیتو تكنولوژي ایتالیاست که داراي 12 درجه آزادي است و موقعیت و گشتاور بندگاه‌هاي آن به‌وسیله بازوهاي هیدرولیكی کنترل می‌گردد\cite{HyQ}. وزن ربات حدود 75 کیلوگرم و داراي یک متر طول و نیم متر عرض است و جثه آن به اندازه یک بز می‌باشد.

سامانه کنترل این ربات بر روي یک کامپیوتر تک بورد
\lr{PC104}
تحت لینوکس زمان واقعی با پچ
\lr{Xenomai} 
 اجراء می‌گردد. این ربات می‌تواند علاوه بر قدم زدن، به‌صورت یورتمه نیز حرکت نماید. شكل
 \ref{ربات هایکیو}
 تصاویري از این ربات را نشان می‌دهد.
    \begin{figure}[!h]
	\centering
	
	\caption[ربات چهارپاي هایكیو]{ربات چهارپاي هایكیو\cite{HyQ}}
	\label{ربات هایکیو}
	\end{figure}
	
\end{itemize}

\section{جمع بندی}
زمینه رباتیک شامل طیف گسترده‌ای از انواع ربات‌ها است، هر کدام برای کاربردها و وظایف خاصی طراحی شده‌اند. از محیط‌های صنعتی تا بهداشت، از کاوش‌ها تا آموزش، ربات‌ها پتانسیل تحول در صنایع را دارند و به شکل‌های مختلفی به زندگی‌های ما اضافه ارزش می‌دهند. با پیشرفت فناوری، انتظار داریم که نوآوری‌های بیشتری را ببینیم و انواع جدیدی از ربات‌ها با قابلیت‌های پیشرفته‌تر پدیدار شوند.
\newpage
\section{ساختار پایان‌نامه}
پایان‌نامه شامل 5 فصل است؛ در فصل اول، ربات و انواع آن با تاکید بر ربات‌های چهارپا، ویژگی‌ها، موارد کاربرد و نمونه‌های پیشین آورده شده است. در فصل دوم، به کمک نرم‌افزار سالیدورکس، قطعات ربات طراحی و ابعاد آن‌ها محاسبه شد. همچنین با بهبود نمونه اولیه سعی در رفع عیوب نموده تا به نمونه نهایی از ربات دست یافته شود. در فصل سوم، تمرکز بر سخت‌افزار ربات شده است و اجزائی مانند سرو موتور، میکروکنترلر، ماژول \lr{Arduino} و دوربین ربات مورد بررسی قرار گرفته است. در فصل بعدی، پروتکل \lr{UART}، تکنیک کنترلی \lr{PWM}، تنظیمات لازم میکروکنترلر در نرم‌افزارهای \lr{CubeMX} و \lr{Keil} انجام شد. در نهایت در فصل پنجم نتیجه‌گیري و پیشنهادات لازم آورده شده است.

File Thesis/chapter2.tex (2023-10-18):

\chapter{طراحی ربات}

\section{مقدمه}
در این فصل شروع به طراحی ربات می‌کنیم که در وهله اول باید طرح و مدل ربات را انتخاب کنیم یا از ابتدا مدل را بسازیم. با توجه به نمونه‌های پیشین که در فصل قبلی به آن‌ها اشاره شد؛ با الگو گرفتن از مدل‌های موجود، مدل ربات را طراحی و آن را می‌سازیم. 
در ادامه برای طراحی از   نرم‌افزار سالیدورکس 
\unskip\LTRfootnote{SolidWorks}
استفاده می‌کنیم که تمام جزئیات و نکات را می‌توان در آن اعمال کرد و درنهایت هم مدل نهایی را پرینت کرده و ربات را اسمبل می‌کنیم. در این مسیر با هربار پرینت قطعات و اسمبل ربات، تمام نکات و ایرادات آشکار شده و برای تست بعدی آن‌ها را برطرف می‌کنیم.
\section{الگوبرداری و انتخاب مدل}
همانطور که در قسمت بالا به آن اشاره شد؛ به دلیل وجود نمونه‌های مشابه و امکان الگوبرداری از آن‌ها، مدلی از ابتدا طراحی نشده و از مدل نمونه‌های ساخته شده، استفاده کردیم. به اصطلاح، ما مدل آزاد
\unskip\LTRfootnote{Free-Model}
اقدام به طراحی ربات کردیم؛ به این معنا است که دیگر درگیر جزئیات و قیدهای مدل نشدیم به این دلیل که هدف اصلی پروژه موضوعی دیگری می‌باشد. در این مسیر با تعدادی ربات چهارپا روبرو شدیم که با توجه به مشخصات مطلوب یعنی وزن مناسب، در حدی که موتورها قادر به بلند کردن و حرکت دادن ربات باشند، ابعاد مناسب، به شکلی که ربات قابلیت حرکت کردن در تمام محیط‌ها را داشته باشد و تنها محدود به محیط‌های باز و بزرگ نباشد، به دلیل امکان پرینت پلاستیکی از الگوهای با جنس فلزی و آهنی نمی‌توان استفاده کرد و درنهایت با توجه به محدودیت هزینه سعی بر ساده یازی مدل تا حد امکان کردیم. از چندین ربات الگو گرفتیم که همگی دارای چهارپا می‌باشند و هر پا دارای 3 درجه آزادی
\unskip\LTRfootnote{DOF(Degree Of Freedom)}
است تا بتواند با آزادی عمل مناسبی به سمت هدف حرکت کند. الگو اصلی که در شکل \ref{ربات چهارپا} مشاهده می‌شود نزدیکترین نمونه به مشخصات مطلوب ما می‌باشد.
    \begin{figure}[!h]	
	\vspace{0.2cm}
	\centering
	
	‌\caption[ربات چهارپا]{ربات چهارپا\cite{Sample}}
	\label{ربات چهارپا}
	\end{figure}

\newpage	
یکی دیگر از نمونه‌هایی که از آن الگو گرفتیم، ربات 
\lr{Titan VIII}
می‌باشد که باز هم دارای چهارپا با سه درجه آزادی می‌باشد اما نحوه جایگیری موتورها با مدل قبلی کمی فرق دارند اما باز هم می‌تواند تمام حرکات لازم را انجام دهد\cite{Titan-VIII}.	
	\begin{figure}[!h]	
	\vspace{0.2cm}
	\centering
	
	‌\caption[ربات چهارپا\lr{Titan VIII}]{ربات چهارپا\lr{Titan VIII}\cite{Titan-VIII}}
	\label{ربات تایتان}
	\end{figure}
	
\section[نرم‌افزار سالیدورکس]{نرم‌افزار سالیدورکس\cite{SolidWoks}}
سالیدورکس یک نرم‌افزار مهندسی طراحی است که بر روی ویندوز اجرا می‌شود و توسط شرکت فرانسوی داسو سیستمز ارائه و همچنان توسعه داده می‌شود. این نرم‌افزار دارای سه محیط به نام‌های پارت
\unskip\LTRfootnote{Part}
،اسمبلی
\unskip\LTRfootnote{Assembly}
و دراوینگ
\unskip\LTRfootnote{Drawing}
می‌باشد. محیط اول برای رسم قطعه بوده، در محیط دوم قطعات یک مکانیسم بر روی هم سوار شده و در محیط آخر از آن‌ها نقشه مهندسی (معمولاً برای نسخه چاپی) تهیه می‌شود.

سالیدورکس یک مدل‌ساز برای مدلسازی جامدات است که مبتنی بر پارا سالید بوده و از رویکرد پارامتری مبتنی بر ویژگی برای ساخت مدل‌ها و مونتاژها استفاده می‌کند. پارامتر به ثابت‌هایی اطلاق می‌شود که مقدار آن‌ها، شکل یا هندسه مدل یا مونتاژ را تعیین می‌کند. پارامترها هم به صورت پارامترهای عددی نظیر طول خطوط یا قطر دایره بوده و هم به صورت قیدهای هندسی نظیر مماس، موازی، متقارب، هم مرکز و غیره هستند. پارامترهای عددی می‌توانند از طریق استفاده روابط با یکدیگر مرتبط بوده که امکان برآورده ساختن خواسته‌های طراحی را فراهم می‌کند. خواسته‌های طراحی به این معناست که طراح مایل است تا مدل نسبت به تغییرات و به روز آوری‌ها به چه صورت پاسخ دهد. مشخصات
\unskip\LTRfootnote{Features}
به عناصر اصلی سازنده قطعات اطلاق می‌شود. مشخصات اشکال و عملیاتی هستند که قطعه را به وجود می‌آوردند. مشخصات، مبتنی بر شکل نظیر برآمدگی‌ها
\unskip\LTRfootnote{Bosses}
،سوراخ‌ها
\unskip\LTRfootnote{Holes}
و غیره معمولاً با یک نقشه دو بعدی یا سه بعدی آغاز می‌شوند.

نرم‌افزار سالیدورکس دارای ویژگی‌های خاصی می‌باشد که آن را از سایر نرم‌افزارهای 
\lr{CAD}\unskip\LTRfootnote{Computer Aided Design}
مانند کتیا
\unskip\LTRfootnote{CATIA(Computer Aided Three-Dimensional Interactive Application)}
،پرو/اینجینیر
\unskip\LTRfootnote{Pro/ENGINEER}
،یونیگرافیکس
\unskip\LTRfootnote{Unigraphics} 
،مکانیکال دسکتاپ
\unskip\LTRfootnote{Mechanical Desktop} 
و اینونتور
\unskip\LTRfootnote{Inventor} 
شاخص و متمایز می‌نماید:
\begin{itemize}
	\item افزایش سرعت و دقت در طراحی
	\item کاهش خطاها و هزینه‌ها
	\item افزایش قابلیت اطمینان از محصول
	\item امکان طراحی پیچیده و ساختارهای مجتمع
	\item افزایش توانایی در حل مسائل
	\item سرعت بالاتر نسبت به سایر نرم‌افزارها
	\item سهولت کاربری و آموزش در مقایسه با سایر نرم‌افزارهای \lr{CAD}
	\item قابلیت ارتباط با تمامی نرم‌افزارهای ماشین کاری \lr{(edge cam, master cam, power mill…)} و نرم‌افزارهای تحلیل \lr{(Ansys, Adams, Abaqus, Cosmos…)}
	\item قابلیت انجام تحلیل‌های مهندسی با اعمال پارامترها به صورت کاملاً ساده و کاربر پسند.
	\item امکان معادله‌نویسی \lr{(Equation)} بین پارامترها و انداز‌ه‌های مختلف در مدل
\end{itemize}

\section{طراحی و محاسبه ابعاد قطعات}
برای طراحی قطعات به دلیل مدل آزاد بودن، روی طراحی کامل قطعات تمرکز نشد بلکه روی جزئیات آن‌ها و بهتر کردن آن‌ها تمرکز کردیم. در طراحی بسیار مهم است که از چه موتوری استفاده می‌شود تا با توجه به آن، ابعاد قطعات را محاسبه کنیم و مشکلی برای جابه‌جایی هر پا و ربات نداشته باشیم.
با توجه به اینکه سروموتور گشتاور \lr{2.5 Kg/cm} دارد، باید به این موضوع توجه شود که موتور اول هر پا باید بتواند تمام قطعات متصل به پا را یعنی دو موتور و سه لینک پا را جابه‌جا کند.

\newpage
\subsection{نمونه اولیه}
براساس همین مشخصات در ابتدا یک بدنه با ابعاد \lr{140*120*4 mm} طراحی کردیم که شامل دو مستطیل با همین ابعاد است که با چهارتا اسپیسر به هم متصل هستند. برای اینکه وزن موتور اول روی بقیه لینک‌ها ایجاد نشود، روی بدنه بالایی جا برای چهار موتور اول هر پا قرار دادیم که روی بدنه ثابت هستند و با استفاده از دیتاشیت 
\unskip\LTRfootnote{Datasheet}
ابعاد سروموتور را بدست آورده و به اندازه آن روی بدنه خالی می‌کنیم و در آخر هم جا برای پیچ‌های آن قرار میدهیم تا ربات موتور در جای خود ثابت شود و جابه‌جایی آن‌ها وابسته به بدنه است و اگر بدنه از موقعیت کنونی به نقطه‌ای دیگر برود آنگاه چهار موتور هم جابه‌جا میشوند. ملاحظاتی دیگر هم درنظر گرفته شده است مانند فاصله اسپیسرها از بدنه که خیلی نزدیک نباشد، چون اگر این اتفاق بیفتد خیلی شکننده شده و امکان باز شدن اسپیسرها وجود دارد. نکته دیگر هم فاصله بین دوتا موتور می‌باشد که باید به نهوی باشد که لینک اول به راحتی بچرخد و به بدنه ربات برخورد نکند. بدنه پایین هم برای قرارگیری قطعات الکتریکی ربات می‌باشد، به همین دلیل باید فاصله مناسبی بین دو بدنه باشد تا قطعات بدون مشکل قرار بگیرند و همچنین سیم 12تا موتور هم باید به بردی که روی بدنه پایین قرار می‌گیرد متصل شود.

	\begin{figure}[!h]	
	\vspace{0.2cm}
	\centering
	
	‌\caption{لایه بالایی و پایینی نمونه اولیه}
	\label{بدنه ربات نمونه اولیه}
	\end{figure}

\newpage	
بعد از بدنه به لینک اول می‌رسیم که ابعاد \lr{50*36*8 mm} و تقریبا وزن 3 گرمی دارد که برای سرو موتور هم مشکلی ایجاد نمی‌کند.(برای محاسبه وزن قطعات از نرم‌افزار \lr{Cura} استفاده کردیم که می‌توان جنس موردنظر و بقیه جزئیات را در آن تنظیم کنیم) که مانند بدنه که موتور لینک اول وزنی روی لینک اضافه نمی‌کند، در اینجا هم وزن موتور دوم روی لینک اول قرار می‌گیرد و هیچ تاثیری روی لینک دوم ندارد. نکته بسیار مهمی که وجود دارد این است که روی لینک باید جایی برای قرارگیری شفت درنظر گرفته شود چونکه شفت موتور دندانه‌دار است و نمی‌توان به لینک اتصال داد که درنهایت بتواند لینک را جابه‌جا کند، پس از شفت‌های موجود در کنار موتور استفاده می‌کنیم تا این مشکل برطرف شود. باز هم مانند بدنه باید برای کوتور بعدی هم از لینک اول خالی کنیم تا در آن قرار بگیرد.

	\begin{figure}[!h]	
	\vspace{0.2cm}
	\centering
	
	‌\caption{لینک اول نمونه اولیه}
	\label{لینک اول نمونه اولیه}
	\end{figure}
	
لینک بعدی هم مانند لینک قبل است فقط ابعاد و شکل آن متفاوت است. ابعاد این لینک \lr{69*36*8 mm} و وزن 3 گرمی می‌باشد. تفاوت اصلی این لینک با لینک قبلی این است که؛ لینک دوم برای اتصال دو موتور دوم و سوم است و برای همین هم دو جا برای شفت در نظر گرفته شده است. مانند دو \lr{U} است که به هم متصل شده‌اند. محور موتور اول و دوم باهم متفاوت و عمود برهم است. یکی از نکات مهم این لینک ابعاد هر \lr{U} است چونکه وقتی موتور دوم جرکت می‌کند، لینک دوم جابه‌جا می‌شود و نباید ابعاد آن به شکلی باشد که به لینک اول گیر بکند یعنی عمق هر \lr{U} باید از فاصله شفت موتور اول تا انتها لینک اول بیشتر باشد.
%(به دلیل آنکه فاصله شفت موتور اول تا ابتدا لینک از انتها کمتر است پس اگر به انتها لینک برخورد نکند قطعا با ابتدا لینک هم برخوردی نخواهد داشت)

	\begin{figure}[!h]	
	\vspace{0.2cm}
	\centering
	
	‌\caption{لینک دوم نمونه اولیه}
	\label{لینک دوم نمونه اولیه}
	\end{figure}
	
در نهایت هم لینک آخر(سوم) را داریم که مشخصات آن \lr{71*15*2 mm} و ا گرم است. چون آخرین لینک پا است دیگر نیازی به طراحی فضایی برای قرارگیری شفت نیست و تنها نیاز است فضایی برای پیچ‌های ربات تعبیه شود تا موتور ثابت در جای حود بماند و نلغزد. چالش موجود برای طراحی این قطعه در نقطه تماس آن با زمین است که باید به شکلی باشد که سطح مقطع مناسبی با زمین در تماس باشد چون اگر کمتر باشد باعث می‌شود ربات به درستی نایستد و بلغزد و اگر بیشتر باشد، پاهای ربات اصطحکاک بیشتر از حد معمول خواهند داشت و به سختی جابه‌جا می‌شوند.

	\begin{figure}[!h]	
	\vspace{0.2cm}
	\centering
	
	‌\caption{لینک سوم نمونه اولیه}
	\label{لینک سوم نمونه اولیه}
	\end{figure}
	
	\begin{figure}[!h]	
	\vspace{0.2cm}
	\centering
	
	\caption{نسخه اولیه ربات}
	\label{نسخه اولیه ربات}
	\end{figure}

\subsection{بهبود مدل}
در ابتدا نمونه اولیه قطعات طراحی و پرینت شدند. سپس با بررسی‌های پیاپی مشکلات و ایرادات فطعات پیدا شده و برای بهبود آن‌ها در طراحی تغییراتی ایجاد شدند. 
  
\begin{itemize}
	\item در ابتدا به بدنه ربات می‌پردازیم؛ تقریبا ابعاد بدنه ثابت مانده است اما تغییراتی در آن اعمال شده است مانند قوسی 
	\unskip\LTRfootnote{Curve}
	کردن گوشه‌های تیز بدنه که هم در استحکام و زیبایی آن تاثیرگذار است. دیگر تغییر مهم طراحی یک \lr{U} است برای قرارگیری موتور در آن برای جایگیری دقیق موتور در مکان دلخواه و همچنین نیاز به یک قطعه مانند شفت موتور تا لینک بین این دو شفت ثابت بماند.
	\item و همچنین اگر سیم 12عدد موتور از پایین به برد وصل شود، ممکن است که پاها به آن‌ها برخورد کرده و به درستی کار نکنند پس برای برطرف کردن این مشکل و همچنین کم کردن وزن بدنه، وسط بدنه بالایی را به اندازه‌ای خالی می‌کنیم تا هم سیم‌ها به راحتی و با قابلیت تفکیک عبور کنند هم اینکه قطعه محکم مانده و شکننده نشود.
	
	\begin{figure}[!h]	
	\vspace{0.2cm}
	\centering
	
	‌\caption{لایه بالایی و پایینی نمونه نهایی}
	\label{بدنه ربات نمونه نهایی}
	\end{figure}
	
	\newpage
	\item اصلی‌ترین مشکلی که با آن مواجه شدیم، دقیق نبودن پرینتر هست. به عنوان مثال جایی که برای قرارگیری موتورها قرار دادیم کوچکتر از اندازه طراحی شده بود و نیاز بود کمی بزرگتر شود. دو روش برای حل این چالش وجود دارد که ابعاد موتور را خیلی بزرگتر وارد کنیم یا مقدار کمی افزایش دهیم. در حالتی که کمی افزایش دهیم شاید باز هم به راحتی موتور در مکان خود قرار نگیرد اما با کمی فشار یا تراشیدن قطعه بتوان آن را جا زد. اما اگر خیلی افزایش ابعاد را داشته باشیم امکان دارد ربات در مکان خود بلغزد.
	\item لینک اول بسیار نازک‌‌تر از قطعه مدنظر بوده است برای همین ابعاد آن تغییر کرده است. مکانی که شفت در آن قرار می‌گیر بزرگتر شده است به این دلیل که شفت فاصله کمی تا بدنه داشته و امکان آسیب دیدن و شکستن قطعه از آن ناحیه وجود داشته است و همچنین شفت به راحتی در آن قرار نمی‌گرفته و به دلیل فشار موتور کمی از جای خود بیرون زده و گاهی اوقات شفت بیرون از قطعه بوده و نتوانسته لینک را تکان دهد. در نهایت هم ماننده بدنه برای ثبات بهتر موتور روی لینک، موتور را در یک محفظه \lr{U} شکل قرار داده شده است. همچنین فاصله سوراخ پیچ تا بدنه هم افزایش داده شده است تا باز هم اصطحکام بالاتر برود. آخرین نکته در این قطعه که در زیبایی و استقامت آن بسیار حائز اهمیت است، قوسی کردن گوشه‌های تیز موجود در لینک است که وظیفه بسیار مهمی در حفظ سلامت قطعه دارد؛ برای مثال قطعه اولیه اگر از بالا و پایین با دست فشرده شود به راحتی می‌شکند و همچنین قابلیت ارتعاشی دارد که اصلا مطلوب و مناسب نیست.
	
	\begin{figure}[!h]	
	\vspace{0.2cm}
	\centering
	
	\caption{لینک اول نمونه نهایی}
	\label{لینک اول نمونه نهایی}
	\end{figure}
	
	\newpage
	\item همانند لینک اول، لینک دوم هم برای جای شفت تغییراتی کرده‌است تا دیگر از جای خود خارج نشده و به درستی عمل کند؛ همچنین گوشه‌های تیز هم قوسی شدند تا در استقامت لینک کمک کنند. سپس تغییری اساسی در آن مشاهده می‌شود که آن هم نحوه اتصال دو \lr{U} می‌باشد که در نمونه اولیه با دو مستطیل کوچک به هم متصل شده‌اند که به شدت شکننده می‌باشد و برای برطرف کردن این مشکل، کل فاصله پر شده‌است و دیگر فضای خالی وجود ندارد. در آخر هم عمق دو تا \lr{U} با هم متفاوت می‌باشد و طرفی که به سمت لینک سوم است کوچکتر از آن طرف قطعه است.
	
	\begin{figure}[!h]	
	\vspace{0.2cm}
	\centering
	
	\caption{لینک دوم نمونه نهایی}
	\label{لینک دوم نمونه نهایی}
	\end{figure}
	
	\item لینک آخر یا همان سوم، کمترین تغییر را نسبت به نمونه اولیه داشته است. ابعاد آن تغییر کرده است تا استحکام بیشتری داشته باشد و همچنین مانند لینک اول قسمتی برای قرارگیری موتور درنظر گرفته شده است.
	
	\begin{figure}[!h]	
	\vspace{0.2cm}
	\centering
	
	\caption{لینک سوم نمونه نهایی}
	\label{لینک سوم نمونه نهایی}
	\end{figure}
	
	\begin{figure}[!h]	
	\vspace{0.2cm}
	\centering
	
	\caption{نسخه نهایی ربات}
	\label{نسخه نهایی ربات}
	\end{figure}
	
\end{itemize}

\subsection{نمونه نهایی}
با بررسی‌های فراوان و بهبود مدل در نهایت قطعات پرینت و ربات اسمبل شده است. بدنه ربات با ابعاد \lr{140*120*4 mm}، لینک اول \lr{140*120*4 mm}، لینک دوم \lr{140*120*4 mm} و لینک سوم هم \lr{140*120*4 mm} قطعی شده‌اند. بعد از چندین دفعه پرینت قطعات و تست آن‌ها به نسخه مطلوب و دلخواه رسیدیم که دیگر مشکل شفت، جای موتور، استقامت و ظاهر نامناسب ربات را نداشته باشیم.

	\begin{figure}[!h]	
	\vspace{0.2cm}
	\centering
	
	
	
	\caption{قطعات پرینت شده ربات}
	\label{قطعات پرینت شده ربات}
	\end{figure}
	
\newpage	
\section{جمع بندی}
در کل، در این مسیر طراحی و ساخت ربات، با تمرکز بر جزئیات و بهبود مداوم در اجزاء و مراحل ساخت، به یک نسخه نهایی از ربات دست پیدا کردیم. با تغییر در ابعاد بدنه و لینک‌ها، حل مشکلاتی مانند جابجایی موتورها و تقویت ساختارها، به یک ربات عملی و قابل اعتماد دست یافتیم. این تجربه نشان می‌دهد که با توجه به دقت در تکنیک‌های مهندسی ساده، می‌توان به اهداف خود در ساخت ربات‌ چهارپا دست پیدا کرد؛ که با استفاده از نرم‌افزار سالیدورکس به این مهم دست پیدا کردیم.
	\vspace{1cm}
	\begin{figure}[!h]	
	\vspace{0.2cm}
	\centering
	
	\caption{ربات اسمبل شده نهایی}
	\label{ربات اسمبل شده نهایی}
	\end{figure}

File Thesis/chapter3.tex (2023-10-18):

\chapter{سخت‌افزار ربات}
\section{مقدمه}
در این قسمت از پایان نامه، به بررسی اجزای اساسی ربات‌ها می‌پردازیم. این اجزا شامل سروموتورها، میکروکنترلرها، بردهای الکترونیکی و سایر قطعات مهم می‌شوند که در ساخت و کنترل ربات‌ها به کار می‌روند. این اجزا با تعامل و همکاری با یکدیگر، امکان حرکت، حسگری و کنترل دقیق را برای ربات‌ها فراهم می‌کنند. در ادامه به بررسی عمیق‌تر هر یک از این اجزا خواهیم پرداخت و نقش آنها در عملکرد کلی ربات‌ها را بررسی خواهیم کرد. همچنین، اهمیت انتخاب و استفاده صحیح از این اجزا را نیز بررسی می‌نماییم. این مقدمه به ما امکان می‌دهد تا به دنیای پیچیده و هیجان‌انگیز رباتیک در عمق بپردازیم و راهنمایی کنیم. 
\section[سرو موتور]{سرو موتور\cite{Servo}}
سروموتورها از جمله اجزاء اساسی در رباتیک و به‌ویژه در ربات‌های چهارپا مورد استفاده قرار می‌گیرند. این اجزا جهت کنترل و حرکت اندام‌ها و پاهای ربات به کار می‌روند. سروموتورها معمولاً دارای یک شفت قابل چرخش هستند که از طریق یک سیگنال کنترلی به جلو و عقب حرکت می‌کنند. سروموتورها به دلیل دقت، سرعت و کاربرد‌های متعددشان، بخش مهمی از طراحی و ساخت ربات‌های چهارپا را تشکیل می‌دهند.

در ربات‌های چهارپا، سروموتورها به‌عنوان موتورهای اصلی برای حرکت پاها و اندام‌ها عمل می‌کنند. این سروموتورها معمولاً دقیق و قابل کنترل با سرعت متغیر هستند، که این ویژگی‌ها امکان جابه‌جایی دقیق و پیچیده را فراهم می‌کنند. سروموتورها معمولاً با استفاده از میکروکنترلرها به راحتی کنترل می‌شوند. این اجزا به تنهایی یا به صورت گروهی در ربات‌های چهارپا استفاده می‌شوند تا حرکت و موقعیت دقیق در سیستم رباتیک تضمین شود.
 
    \begin{figure}[!h]
	\centering
	\vspace{1cm}
	
	\caption{سرو موتور \lr{SG90}}
	\label{سرو موتور}
	\end{figure}

\subsection{اجزای سرو موتور}
یک سرو موتور از سه قسمت اصلی تشکیل شده است:

1. \textbf{موتور}: موتور بسته به منبع تغذیه و نیازهای برنامه کاربردی، ممکن است یک موتور جریان مستقیم
\unskip\LTRfootnote{DC motor}
یا موتور جریان متناوب
\unskip\LTRfootnote{AC motor}
باشد که قدرت مکانیکی را برای چرخش یا حرکت شفت خروجی فراهم می‌کند.

2. \textbf{حسگر}: می‌تواند یک پتانسیومتر، یک انکودر، یک رزولور یا دستگاهی دیگر باشد که موقعیت، سرعت یا گشتاور شفت خروجی را اندازه‌گیری کرده و سیگنال‌های بازخورد را به کنترل‌کننده ارسال می‌کند.

3. \textbf{کنترل‌کننده}: می‌تواند یک مدار آنالوگ یا دیجیتال باشد که سیگنال‌های بازخورد از حسگر را با سیگنال‌های مقدار مورد نظر از یک منبع خارجی (مانند یک کامپیوتر یا یک جوی استیک
\unskip\LTRfootnote{Joystick}
) مقایسه کرده و سیگنال‌های کنترلی را تولید کرده تا ولتاژ یا جریان موتور را به تناسب تنظیم کند. کنترل‌کننده از یک سیستم بازخورد حلقه بسته
\unskip\LTRfootnote{Closed-Loop}
استفاده می‌کند تا حرکت موتور را تنظیم کرده و اطمینان حاصل کند که با مقدار مورد نظر تا حدود خطای مشخصی همخوانی دارد. کنترل‌کننده همچنین می‌تواند از انواع مختلفی از الگوریتم‌های کنترل استفاده کند، مانند کنترل
\lr{PID}
، کنترل منطق فازی
\unskip\LTRfootnote{Fuzzy logic control}
، کنترل تطبیقی
\unskip\LTRfootnote{Adaptive control}
و غیره، به منظور بهینه‌سازی عملکرد موتور سرو.
\subsection{انواع سرو موتور}

موتورهای سرو بر اساس منابع تغذیه، ساختار، مکانیزم بازخورد و کاربردهای خود به انواع مختلفی تقسیم می‌شوند.

1-\textbf{موتورهای سرو جریان متناوب}
\lr{(AC)} 

سرو موتورهای متناوب به دو نوع سنکرون و آسنکرون تقسیم می‌شوند:
\begin{itemize}
\item
سرو موتورهای متناوب سنکرون: دارای یک روتور با آهنربای دائمی هستند که با سرعت مشابه میدان استاتور می‌چرخند. آن‌ها ، دقیق‌تر و پاسخ‌گویی بهتری نسبت به موتورهای آسنکرون دارند، اما به کنترل‌کننده پیچیده‌تری و یک حسگر موقعیت نیاز دارند.
\item
سرو موتورهای متناوب آسنکرون: دارای یک روتور کلافی یا روتور سیم‌پیچی هستند که یک جریان القاء می‌کنند و یک میدان مغناطیسی دارند که عقب‌‌تر از میدان استاتور است. آن‌ها ساده‌تر، ارزان‌تر و مقاوم‌تر از موتورهای سنکرون هستند، اما کارایی، دقت و سرعت پایین‌تری دارند.

سرو موتورهای متناوب برای کاربردهایی با نیاز به توان بالا، سرعت و قابلیت اطمینان مناسب هستند و به طور معمول در دستگاه‌های صنعتی، رباتیک، دستگاه‌های 
\lr{CNC} 
و غیره استفاده می‌شوند.

2-\textbf{موتورهای سرو جریان مستقیم}
\lr{(DC)}

سرو موتورهای جریان مستقیم از جریان مستقیم
\lr{(DC)} 
برای تغذیه خود استفاده می‌کنند. آن‌ها دارای یک استاتور با آهنربای دائمی هستند که یک میدان مغناطیسی ثابت ایجاد می‌کند و یک روتور کلافی دارند که هنگامی که جریانی به آن داده می‌شود، می‌چرخد.

موتورهای سرو جریان مستقیم به دو نوع با جاروبک
\unskip\LTRfootnote{Brushed}
و بدون جاروبک
\unskip\LTRfootnote{Brushless}
 تقسیم می‌شوند.
\item
سرو موتورهای جریان مستقیم با جاروبک: دارای یک کموتاتور
\unskip\LTRfootnote{Commutator}
و جاروبک‌هایی است که جهت جریان را در مارپیچ‌های روتور تغییر می‌دهند. آن‌ها ساده، ارزان و با کنترل آسان هستند، اما به دلیل اصطکاک و سایش تراشه‌ها کارایی، عمر مفید و سرعت پایین‌تری دارند.
\item
سرو موتورهای جریان مستقیم بدون جاروبک: دارای یک کنترل‌کننده الکترونیکی هستند که جهت جریان را در مارپیچ‌های استاتور تغییر می‌دهند. آن‌ها از لحاظ کارایی، مقاومت و سرعت، نسبت به موتورهای تراشه بهتر هستند، اما نیاز به کنترل‌کننده پیچیده‌تر و یک حسگر موقعیت دارند.

سرو موتورهای جریان مستقیم مناسب برای کاربردهای با توان پایین که نیاز به دقت بالا، پاسخگویی و حرکت نرم دارند، هستند و به طور معمول در پروژه‌های سرگرمی، اسباب‌بازی‌های اتومبیل‌، پخش‌کننده‌های
\lr{CD/DVD} 
و غیره استفاده می‌شوند.

در این پروژه برای ساخت ربات چهارپا، با توجه به قابلیت ها و ویژگی ها از موتور جریان مستقیم بدون جاروبک استفاده شده است.
\end{itemize}

\newpage
\section{میکروکنترلر}

میکروکنترلر
\unskip\LTRfootnote{Microcontroller} 
در اصل یک چیپ الکترونیکی برنامه‌پذیر است که با اتصال قطعات مختلف در یک مدار الکترونیکی، اجزای یک کامپیوتر ساده را فراهم می‌کند. از میکروکنترلر برای ساخت، کنترل و مانیتورینگ انواع سیستم‌های الکترونیکی استفاده می‌شود که با برنامه‌ریزی واحدهای میکروکنترلر و تجهیزات جانبی فعال می‌گردد. میکروکنترلر شامل
\lr{CPU}
، حافظه
\lr{RAM/ROM}
، پورت‌های ورودی و خروجی
\lr{(I/O)}
، تایمر، مبدل آنالوگ به دیجیتال
\unskip\LTRfootnote{ADC}
و مبدل دیجیتال به آنالوگ
\unskip\LTRfootnote{DCA}
است.
\lr{CPU}
درواقع همان مغز میکروکنترلر است، که وظیفه‌ی استخراج و پردازش داده ها، انجام محاسبات و وظایف اختصاص­‌داده شده را بر عهده دارد. تایمر برای تولید پالس، اندازه­‌گیری فرکانس و ساخت نوسانات به‌کار می‌رود تا عملیات زمان‌بندی و شمارش را کنترل نماید.

برای برنامه نویسی میکروکنترلر ها ، نرم افزار های خاصی وجود دارند که به آن ها کامپایلر
\unskip\LTRfootnote{Compiler}
می‌گویند. چند تا از کامپایلر های محبوب کیل \lr{(Keil)}، اتمل استودیو \lr{(Atmel Studio)}، کدویژن \lr{(Codevision)} و بسکام \lr{(Bascom)} هستند. 
در هر کامپایلر برنامه نویسی به زبان / زبان های خاصی انجام می‌شود. به طور مثال در کامپایلر کیل از زبان های \lr{C} و اسمبلی (\lr{Assembly}) استفاده می‌شود\cite{Electronics}.

برای استفاده مناسب و صحیح از این قطعه الکترونیکی، باید ابتدا با انواع میکرو کنترلر و کاربردهای آن آشنا شد.

    \begin{figure}[!h]
	\centering
	
	\caption[اجزای میکروکنترلر]{اجزای میکروکنترلر\cite{Micro}}
	\label{اجزا میکرو}
	\end{figure}

\newpage	
\subsection{انواع میکروکنترلر}
اغلب میکروکنترلرها ویژگی‌های مشترک زیادی دارند زیرا همه‌ی آنها دارای یک حافظه درایو، پایه‌های ورودی و خروجی و توان مصرفی کم  هستند. اما در جزِئیاتی مانند تعداد پایه‌ها، ابعاد، قیمت تمام شده و غیره نیز با هم متفاوت‌اند.
میکروکنترلرها براساس حافظه، معماری، بیت‌ها و مجموعه دستورالعمل‌ها به دسته بندی‌های مختلفی تقسیم می‌شوند. در اینجا انواع میکروکنترلرها براساس نوع کارکرد و مداری که در آن ها مورد استفاده قرار می‌گیرند به گروه‌های زیر دسته بندی می‌شوند:
\begin{itemize}
\item
میکروکنترلرهای \lr{AVR}
\item
میکروکنترلرهای  \lr{ARM}
\item
میکروکنترلرهای  \lr{XMEGA}
\item
میکروکنترلرهای  \lr{PIC}
\item
میکروکنترلرهای 8051
\end{itemize}

    \begin{figure}[!h]
	\centering
	
	\caption[انواع میکروکنترلر]{انواع میکروکنترلر\cite{Micro}}
	\label{انواع میکرو}
	\end{figure}

\newpage
\subsection{مزایا}
ميكروكنترلرها داراي مزاياي متعدد هستند. مزیت فوق العاده میکروکنترلر ها کم شدن تعداد آی‌سی‌ها و قابلیت چند بار نوشتن و پاک کردن کد است.در ذیل چند مزیت مهم میکروکنترلرها آورده شده‌است:

1. \textbf{سهولت برنامه‌نویسی}: ميكروكنترلرها با زبان‌هاي برنامه‌نويسي ساده و قابل فهم برنامه‌ريزي مي‌شوند.

2. \textbf{حجم کم}: ابعاد كوچك ميكروكنترلرها، امكان استفاده در دستگاه‌هاي با اندازه کوچک را فراهم مي‌كند.

3. \textbf{مصرف انرژی پایین}: ميكروكنترلرها از انرژي كمي براي عملكرد خود استفاده مي‌كنند.

4. \textbf{انعطاف‌پذيري}: اين دستگاه‌ها قابليت تغيير برنامه‌هاي خود را دارا هستند و مي‌توان آن‌ها را براي بسياري از كاربردها برنامه‌ريزي كرد.

5. \textbf{هزينه پايين}: ميكروكنترلرها به صورت معمول به صورت اقتصادي قابل تهيه هستند و در اكثر موارد ارزان‌ترين گزينه براي كنترل دستگاه‌ها هستند.

6. \textbf{سرعت بالا}: اين دستگاه‌ها با سرعت بالايي عمل مي‌كنند و گاهی نياز به پردازش سريع دارند.

7. \textbf{قابليت ارتباطات}: ميكروكنترلرها قابليت ارتباط با ساير دستگاه‌هاي الكترونيكي را فراهم مي‌كنند.

8. \textbf{پايداري}: اين دستگاه‌ها داراي پايداري و اطمينان بالايي در عملكرد خود هستند.

با توجه به اين مزايا، ميكروكنترلرها ابزاري قدرتمند براي كنترل و اتوماسيون در صنايع و كاربردهاي الكترونيكي هستند.

\subsection{کاربرد}
همان‌طور که اشاره شد، میکروکنترلر در اصل یک رایانه بسیار کوچک است که در هر پروژه و دستگاهی به طور همزمان نقش قلب و مغز مجموعه را ایفا می‌کند. بنابراین در حال حاضر در بیشتر لوازم خانگی و دستگاه‌های پزشکی و صنعتی مانند سیستم کنترل روشنایی، سیستم کنترل دما و آتش، سیستم‌های کنترل فرمان که در آنها اعمالی همچون اندازه‌گیری، ذخیره‌سازی، محاسبه، کنترل و نمایش اطلاعات انجام می‌شود، از میکروکنترلر استفاده شده است. 
    \begin{figure}[!h]
	\centering
	
	\caption[کاربردهای میکروکنترلر]{کاربردهای میکروکنترلر\cite{Micro}}
	\label{کاربرد میکرو}
	\end{figure}

با توجه به تمام نکات در ابتدا قصد به استفاده از ماژول \lr{Arduino Uno} داشتیم اما به این دلیل که ما برای کنترل هر موتور به یک پایه با قابلیت \lr{PWM} نیاز داریم تصمیم به استفاده از ماژول \lr{STM32F103C8T6} گرفتیم که تمام خواسته‌های ما را برطرف می‌کند.
\section{ماژول \lr{STM32F103C8T6}}
میکروکنترلر \lr{STM32F103C8T6} دارای هسته پردازنده 32 بیتی\lr{ARM Cortex M3 } توسط شرکت \lr{STMicroelectronics} ساخته شده است است. این برد شامل میکروکنترلر \lr{STM32F103C8T6}، پورت میکرو \lr{USB} تغذیه، دکمه \lr{Reset}، دو سلکتور \lr{BOOT0} و \lr{BOOT1}، کریستال \lr{8MHz}، کریستال \lr{RTC 32.768KHz}، دو \lr{LED} (یک \lr{LED} نمایش دهنده اتصال تغذیه و دیگری متصل به پین \lr{C13} برای استفاده کاربر)، رگولاتور \lr{3.3V} و هدر برد پایه‌های \lr{SWI} برای پروگرام کردن میکرو است.

مشخصات فنی ماژول موردنظر:
\begin{itemize}
	\item دارای هسته 32 بیتی \lr{ARM Cortex M3}
	\item ولتاژ کاری: 7.2 تا 6.3 ولت
	\item فرکانس: ماکزیمم 72 مگاهرتز
	\item حافظه: 64 کیلوبایت
	\item تعداد پین‌های ورودی/خروجی: 37
	\item تعداد پین‌های \lr{PWM}: 4 + 12
	\item تایمر: 3+1
	\item پروتکل های ارتباطی: \lr{I2C, SPI, UART/USART}
\end{itemize}

    \begin{figure}[!h]
	\centering
	
	\caption{ماژول \lr{STM32F103C8T6}}
	\label{STM32}
	\end{figure} 

\section{ماژول \lr{Arduino-Uno}}

برد  \lr{Arduino Uno}، یک برد متن‌باز مبتنی بر میکروکنترلر   \lr{Microchip ATmega328P} است و توسط شرکت \lr{Arduino.cc} ساخته شده است. این برد مجهز به مجموعه‌ای از پین‌های ورودی / خروجی دیجیتال و آنالوگ است که می‌تواند به راحتی با شیلدهای آردوینو ارتباط برقرار کند. برد \lr{Uno} اولین سری از سری برد های آردوینو مبتنی بر \lr{USB} است. میکروکنترلر \lr{ATmega328} موجود در برد با یک بوت لودر از قبل برنامه ریزی شده است که اجازه می دهد بدون استفاده از پروگرمر سخت افزاری خارجی برنامه‌ریزی شود. ماژول آردوینو اونو در زیر آورده شده است:

    \begin{figure}[!h]
	\centering
	
	\caption{ماژول \lr{Arduino Uno}}
	\label{Arduino}
	\end{figure} 
برای پروگرم کردن ماژول \lr{ESP32-CAM} نیاز داریم که با استفاده از پروتکل سریال این کار را انحام دهیم و برای انجام آن از \lr{FTDI} استفاده می‌کنیم که رابط سریال به \lr{USB} می‌باشد. اما ما به‌جای آن از ماژول \lr{Arduino Uno} استفاده می‌کنیم هم به دلیل دردسترس بودن، سادگی و توانایی مشاهده اطلاعاتی که از دوربین برای ما فرستاده می‌شود؛ مانند متصل بودن یا نبودن به روتر و \lr{IP} که دوربین روی آن بالا آمده‌است.
\section{ماژول \lr{ESP32-CAM}}

ماژول \lr{ESP32-CAM} یک ماژول کامل با میکروکنترلری یکپارچه است که می‌تواند به‌طور مستقل کار کند. علاوه بر اتصال اینترنت و بلوتوث، دارای یک دوربین فیلمبرداری یکپارچه و یک کارت حافظه \lr{microSD} برای ذخیره سازی است. این قطعه برای نظارت و شناسایی تصویر بسیار کاربردی است.

مشخصات فنی این ماژول به شرح زیر است:
\begin{itemize}
\item 
ارتباطات: بلوتوث \lr{BLE 4.2} به همراه \lr{WiFi 802.11b}. که از بارگذاری تصویر از طریق \lr{WiFi} پشتیبانی می کند.
\item
اتصالات: \lr{UART} ، \lr{SPI} ، \lr{I2C}، و \lr{PWM} و دارای 9 پایه \lr{GPIO} است.
\item
فرکانس کاری: تا 160 مگاهرتز
\item
حافظه: 520 کیلوبایت \lr{SRAM}، چهار مگابایت حافظه کارت \lr{PSRAM + SD}
\item
دوربین: از دوربین های \lr{OV2640} پشتیبانی می‌کند که دارای 2 مگاپیکسل روی سنسور با اندازه آرایه  1622 × 1200\lr{UXGA} پیکسل هستند.
\end{itemize}

    \begin{figure}[!h]
	\centering
	
	\caption{ماژول \lr{ESP32-CAM}}
	\label{ESP32}
	\end{figure} 

\section{منبع تغذیه دی سی}

منبع تغذیه را می‌توان اینگونه تعریف کرد که یک وسیله الکتریکی است که برای تامین برق بارهای الکتریکی استفاده می شود. وظیفه اصلی این دستگاه تغییر جریان الکتریکی از منبع به ولتاژ، فرکانس و جریان دقیق برای تامین بار می‌باشد. منبع تغذیه دی‌سی
\lr{DC}
\unskip\LTRfootnote{Direct Current}
 منبع تغذیه ای است که ولتاژ دی‌سی ثابتی را برای بار خود فراهم می‌کند. منبع تغذیه \lr{DC} که به عنوان منبع تغذیه میزی نیز شناخته می‌شود، نوعی منبع تغذیه است که ولتاژ جریان مستقیم \lr{(DC)} را برای تغذیه یک دستگاه تامین می‌کند.
 
 در این پروژه، علت استفاده از منبع ولتاژ دی‌سی به جای باتری، کاهش وزن ربات، توان خروجی بالا و عملکرد پایدارتر است. 
 
    \begin{figure}[!h]
	\centering
	
	\caption{منبع ولتاژ \lr{DC}}
	\label{منبع ولتاژ}
	\end{figure} 

\section{برد الکترونیکی}

بردهای الکترونیکی شامل \lr{Breadboard}، برد مدارچاپی 
\unskip\LTRfootnote{PCB}
و برد‌ 1000 سوراخ
\unskip\LTRfootnote{Stripboard}
هستند. این ابزارها به عنوان پایه‌هایی برای ساخت و اتصال مدارهای الکترونیکی عمل می‌کنند و در جنبه‌های عملکردی متفاوتی دارند. در زیر توضیح مختصری از هرکدام ارائه شده است:

\subsection{\lr{Breadboard}}
بردبورد وسیله‌ای است که می‌توان با استفاده از آن بدون لحیم کاری نمونه‌های اولیه مدارهای الکترونیکی را طراحی و تست نمود. با قرار دادن پایه های قطعات الکترونیکی در سوراخ ها و سپس برقراری اتصال به وسیله سیم در مدار های الکترونیکی به یکدیگر وصل می‌شوند. بردبورد نوارهای فلزی دارد که در زیر سوراخ‌های پلاستیکی قرار گرفته و آن‌ها را به هم متصل می‌کند. سوراخ‌های ردیف‌های بالا و پایین به صورت افقی متصل هستند و به وسیله شیاری در وسط تقسیم می‌شوند در حالی که سوراخ‌های باقی مانده به صورت عمودی متصل هستند.
    \begin{figure}[!h]
	\centering
	
	\caption{\lr{Breadboard}}
	\label{برد بورد}
	\end{figure} 
\subsection{برد \lr{PCB}}

برد مدار چاپی یا \lr{PCB}
\unskip\LTRfootnote{Printed Circuit Board}
یک برد  غیررسانا و چندلایه مسی است که تمامی قطعات الکتریکی و الکترونیکی از طریق یک برد مشترک و به‌وسیله تکیه‌گاه فیزیکی نصب شده در کف برد به یکدیگر متصل‌اند. قبل از رشد و گسترش بردهای مدار چاپی، مدار ها به‌وسیله سیم‌کشی نقطه به نقطه ساخته می شدند که باعث افزایش پیچیدگی و عدم اطمینان در مدار می‌شد. در نتیجه هیچ‌گاه (بوسیله اتصال قطعات با سیم) قادر به ساخت مدار بزرگی نبودیم. در برد مدار چاپی تمامی قطعات بدون سیم و از داخل به یکدیگر متصل‌اند که این ویژگی منجر به کاهش پیچیدگی طرح کلی مدار می‌شود.روش طراحی \lr{PCB} به گونه‌ای است که  در فراهم کردن الکتریسیته و اتصال بین قطعات مدار کاربرد ویژه‌‌ای دارد.

    \begin{figure}[!h]
	\centering
	
	\caption{یک نمونه برد مدار چاپی}
	\label{مدار چاپی}
	\end{figure} 

\subsection{هزار سوراخ}

برد هزار سوراخ‌
\unskip\LTRfootnote{Stripboard}
گزینه دیگری است که می‌توان هنگام ساخت برد مدار برای پروژه الکترونیکی در نظر گرفت. این بردها برای نمونه‌سازی و تولید بردهای مدارهای کاربردی عالی هستند.بردهای هزار سوراخ با سوراخ‌های مشبک مستطیلی 0.1 اینچی و نوارهای مسی موازی در یک طرف مشخص می‌شوند. قطعات الکترونیکی باید روی این بردها لحیم شوند. با توجه به سوراخ 0.1 اینچی، به قطعاتی با پین‌های 0.1  اینچی نیاز است. قطعات همیشه در یک طرف بورد قرار می‌گیرند، در حالی که انتهای پایه آ‌ن‌ها در انتهای دیگر بیرون می‌آید. سپس محل برخورد برد و پایه قطعات باید لحیم شوند. لحیم‌کاری باید به‌گونه‌ای باشد که اطمینان حاصل شود که پایه‌ها به مسیرهای مسی در طرف دیگر نوار وصل هستند. در مواردی که نیاز به اتصال سیم است، استفاده از سیم‌های 0.1 اینچی توصیه می‌شود. بردهای هزار سوراخ برای ساخت مدارهای کوچک عالی هستند اما محدودیت‌هایی نیز دارند.

    \begin{figure}[!h]
	\centering
	
	\caption{یک نمونه برد هزار سوراخ}
	\label{برد هزار سوراخ}
	\end{figure} 
	
	در این پروژه، با توجه به بودجه مالی و امکانات، استفاده از برد هزار سوراخ بهترین گزینه ممکن است.

\section{جمع بندی}
با بررسی تمام نکات و نیازهای ما برای انجام هرچه بهتر این پروژه، درنهایت بهترین انتخاب برای هر قطعه را با توجه به محدودیت مالی و زمانی انجام دادیم. نکته بسیار مهم که در آخر باید به آن اشاره شود این است که به این مسئله که آیا تمام قطعات با یکدیگر می‌توانند کار کنند و همان عملکری که از آن‌ها توقع داریم را برآورده کنند یا خیر. به عنوان مثال ما در ابتدا قصد استفاده از \lr{Arduino Uno} داشتیم اما به دلیل نیاز به 12 پایه با قابلیت \lr{PWM} از ماژول \lr{STM32F103C8T6} استفاده کردیم.

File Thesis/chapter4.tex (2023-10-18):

\chapter{نرم‌افزار و الگوریتم‌های مورد استفاده}
\section{مقدمه}
در این فصل بعد از طراحی و ساخت قطعات ربات و سپس اسمبل کردن آن به بحث نرم‌افزاری پروژه می‌پردازیم. در ابتدا با چند پروتکل و تکنیک آشنا می‌شویم که در مسیر انجام دقیق پروژه از آن‌ها استفاده می‌کنیم که عبارت است از 
\lr{UART} و \lr{PWM}.
به دلیل استفاده از میکروکنترلر \lr{STM32}، تنظیمات اصلی و پایه‌های آن را در نرم‌افزار  \lr{CubeMX} انجام می‌دهیم و در ادامه در محیط  \lr{Keil} شروع به برنامه‌نویسی روی میکروکنترلر می‌کنیم. برای مرتب شدن کد سعی کردیم تا جایی که امکان دارد هر قسمت کد را جدا کرده و به صورت تابع بنویسیم. در نهایت هم با بررسی‌های فراوان، چهار حرکت اصلی ربات را بدست آوردیم.
\section{پروتکل \lr{UART}}
پروتکل‌های ارتباطی نقش مهمی را در سازماندهی ارتباطات بین دستگاه‌های مختلف بازی می‌کنند. این پروتکل ها بر اساس نیازهای هر سیستم در حالت‌های متفاوتی طراحی شده‌اند و با تعریف قوانین مشخص که در دستگاه‌های مختلف مشترک می‌باشد می‌توانند ضامن یک ارتباط موفق و پایدار در شبکه باشند.

سیستم‌های جاسازی شده، میکروکنترلرها و کامپیوترها غالباً از \lr{UART} به عنوان پروتکلی سخت افزاری برای برقراری ارتباط بین دستگاه‌های مختلف استفاده می‌کنند. در میان پروتکل‌های سخت افزاری موجود، \lr{UART} برای ارسال و دریافت داده تنها از دو سیم بهره می‌برد.

\lr{UART}
مخفف
\lr{Universal Asynchronous Receiver-Transmitter}
به معنی فرستنده و گیرنده سریال ناهمزمان جهانی است. دو سیگنال در هر \lr{UART} به صورت زیر نام گذاری می‌شود:
    \begin{figure}[!h]
    \centering
	
	\caption[سیگنال های فرستنده گیرنده \lr{UART}]{سیگنال های فرستنده گیرنده \lr{UART}}
	\label{سیگنال فرستنده و گیرنده}
	\end{figure}
	
بخش فرستنده \lr{UART} به یک باس کنترل‌کننده داده‌ها متصل شده و اطلاعات به صورت موازی به کنترل کننده ارسال می‌شود، سپس داده‌ها به صورت سریال و بیت به بیت روی خط انتقال (سیم) برای گیرنده \lr{UART} فرستاده می‌شوند. گیرنده \lr{UART} نیز داده‌های سریال را پیش از انتقال به گیرنده اصلی به صورت موازی درمی آورد.

\newpage
در‌واقع خطوط \lr{UART} یک نوع واسط ارتباطی هستند که اطلاعات را از یک دستگاه می‌گیرند و به دستگاهی دیگر انتقال می‌دهند که پروتکل \lr{UART} پین هایی منحصر به فرد را به انتقال یا دریافت داده اختصاص داده و یک پین نمی‌تواند هم خروجی و هم ورودی باشد.

    \begin{figure}[!h]
	\centering
	
	\caption[رابط سریال \lr{UART}]{رابط سریال \lr{UART}}
	\label{رابط سریال}
	\end{figure}

ما برای برقراری ارتباط بین \lr{STM32} و \lr{ESP32} از پروتکل \lr{UART} استفاده می‌کنیم به این دلیل که ما از 12پایه که قابلیت \lr{PWM} دارند استفاده کردیم و تنها پروتکل موجود برای برقراری ارتباط \lr{UART} می‌باشد.

\section{تکنیک کنترلی \lr{PWM}}
\subsection{مفهوم \lr{PWM}}
در بسياري از موارد، ما نياز به كنترل ولتاژ بر روي پايه‌هاي خروجي ميكروكنترلر را داريم. مثلاً اگر بخواهيم سرعت موتور را كنترل كنيم، بايد ولتاژي كه بر روي موتور اعمال مي‌شود را كنترل كرد. در حقيقت سرعت موتور تقريباً تابع مستقيمي از ولتاژي است كه بر روي آن اعمال مي‌شود. يعني اگر ولتاژ كاريِ موتوري (ولتاژ استاندارد براي فعال سازي موتور كه بر روي بدنه‌ي آن نوشته مي‌شود) 12 ولت باشد، با اعمال ولتاژ 6 ولت روي آن، مي‌توانيد سرعت چرخش آن (\lr{rpm}\LTRfootnote{Rounds Per Minute}) را حدوداً به نصف كاهش دهيد.

\lr{PWM} مخفف \lr{pulse width modulation} یک فرآیند یا تکنیک مدولاسیون است که
در اکثر سیستم های ارتباطی برای کدگذاری دامنه سیگنال در عرض پالس یا مدت زمان سیگنال، معمولاً سیگنال حامل، به منظور انتقال استفاده می شود.

\lr{PWM} به ما این امکان را می دهد تا مدت زمان سیگنال را به صورت آنالوگ زیاد کنیم. در حالی که سیگنال در هر زمان فقط می تواند \lr{High} (معمولاً 5 ولت) یا \lr{Low} (زمین) باشد، ما می توانیم نسبت زمان \lr{High} بودن سیگنال را در مقایسه با زمانی که سیگنال \lr{Low} است در یک فاصله زمانی ثابت تغییر دهیم.

یکی از مفاهیم اساسی در فهم این که \lr{PWM} چیست، چرخه کار یا همان \lr{duty cycle} است. چرخه کار بر حسب درصد اندازه گیری می شود. چرخه کار به طور مشخص درصد زمانی را که سیگنال دیجیتال در یک بازه یا دوره زمانی روشن است، توصیف می کند. این دوره معکوس فرکانس شکل موج است.

اگر سیگنال دیجیتالی نیمی از زمان را روشن و نیمی دیگر را خاموش باشد، ما می گوییم که سیگنال دیجیتال دارای چرخه کار \lr{٪}50 می باشد که شبیه یک موج مربعی ایده آل است. اگر درصد بیشتر از 50 باشد، سیگنال دیجیتال زمان بیشتری را در حالت بالا نسبت به حالت پایین می گذراند و برعکس اگر چرخه کار کمتر از 50 باشد، در این جا یک نمودار وجود دارد که این سه سناریو را نشان می دهد:
    \begin{figure}[!h]
	\centering
	
	\caption[چرخه کار\lr{Duty Cycle}]{چرخه کار\lr{Duty Cycle}}
	\label{چرخه کار}
	\end{figure}

\subsection{کاربرد \lr{PWM} در سروموتور}
با این قابلیت می‌توان سرعت و یا مکان ربات را کنترل کرد. که در سروموتور با توجه به وجود برد کنترلی بر روی آن قادر هستیم زاویه چرخش شفت موتور را کنترل کنیم و با این کار می‌توانیم هر پا که دارای سه لینک است را به هر جهت دلخواه حرکت دهیم چون محور دو موتور موازی هستند اما محور موتور دیگر عمود بر بقیه هست و همین باعث می‌شود محدوده زیادی را پوشش دهد.

با توجه به دیتاشیت موتور \lr{SG90}، این موتور دارای فرکانس 50 هرتز می‌باشد پس هر دوره تناوب آن برابر با 20 میلی ثانیه است. چرخه کاری این نوع موتور که در شکل \ref{SG90} آمده است، بین 1 تا 2 میلی ثانیه (در بعضی مواقع 5.0 تا 5.2 ثانیه) است که باعث می‌شود شفت از زاویه 0 تا 180 تغییر کند. به این صورت که اگر چرخه کار کمتر از 1 میلی ثانیه یا بیشتر از 2 میلی ثانیه باشد هیچ تغییری ایجاد نمی‌کند.

برای شفاف شدن این موضوع باید به این مورد اشاره کنیم که به صورت خطی بین چرخه کار 1 تا 2 میلی ثانیه (در بعضی مواقع 5.0 تا 5.2 ثانیه) و زاویه 0 تا 180 رابطه‌ای وجود دارد. به این صورت که اگر چرخه کار 1 میلی ثانیه باشد موتور در 0 درجه خود قرار دارد و اگر 5.1 میلی ثانیه باشد در 90 درجه و در نهایت اگر در 2 میلی ثانیه باشد در 180 درجه قرار دارد(شکل \ref{SG90})؛ پس ما به تمام زوایا دسترسی خواهیم داشت با توجه به این که تغییر هر زاویه تقریباً با 55.5 میکرو ثانیه معادل است.

    \begin{figure}[!h]
	\centering
	
	
	\caption[فرکانس و دوره تناوب \lr{SG90}]{فرکانس و دوره تناوب \lr{SG90}}
	\label{SG90}
	\end{figure}
	
\section{نرم‌افزار \lr{CubeMX}}
\subsection{مفهوم وکاربرد}
نرم افزار \lr{STM32CubeMX} که به اختصار به آن \lr{CubeMX} -کیوب ام ایکس- نیز می‌گویند، به جهت ساده‌تر کردن و سرعت بخشیدن به برنامه نویسی میکروکنترلرهای \lr{STM32} ایجاد شده است. ایجاد پروژه و راه‌اندازی واحدهای مختلف میکروکنترلرهای \lr{STM32} به صورت گرافیکی از جمله مهم‌ترین وظایف این نرم‌افزار است. اگرچه کارکردهای دیگری چون تخمین میزان مصرف توان میکروکنترلر را نیز دارد.

\subsection{کتابخانه‌های برنامه‌نویسی}
این نرم‌افزار، درون خود متناسب با هر میکروکنترلر شرکت  \lr{ST}، کتابخانه‌هایی چون \lr{HAL, LL, USB, TCP/IP} و ..   را دارا می‌باشد، که در صورت لزوم آن‌ها را به پروژه ما اضافه می‌کند. لایه \lr{HAL} از یک سمت با سخت‌افزار و از یک سمت با سطوح بالاتر از خود که می‌تواند \lr{Middleware} یا برنامه کاربر باشد ارتباط برقرار می‌کند. البته اگر بیان دقیق‌تر موردنظر باشد کتابخانه \lr{CMSIS} نیز باید در نظر گرفته شود که خود رابط \lr{HAL} با هسته \lr{ARM} مورد استفاده در میکروکنترلر خواهد بود.

این نرم‌افزار علاوه بر فراهم کردن محیط تصویری و قابلیت فعال کردن و انجام اکثر تنظیمات به صورت گرافیکی این امکان را می‌دهد که کاربر یک دید کلی نسبت به میکروکنترلر خود داشته باشد و مناسب‌ترین میکروکنترلر برای کار خود را انتخاب کند.

\newpage
با استفاده از این نرم افزار کتابخانه های \lr{HAL} و \lr{LL} به طور خودکار و بسته به انتخاب هایی که انجام شده باشد به کد اضافه می‌شود. همچنین مقداردهی‌های اولیه و بعضی از تنظیمات به صورت خودکار انجام می‌شود.
\begin{itemize}
	\item \textbf{توابع \lr{(Low Layer)LL}}: در این روش دیگر به‌صورت مستقیم با رجیسترها کار نمی‌شود و فقط از توابعی به نام توابع \lr{LL} استفاده خواهد شد که خود این توابع با توجه به آرگومان‌های ورودی‌شان، رجیسترها را مقداردهی می‌کنند. با فراخوانی هرکدام از این توابع عملاً بخشی از یک واحد جانبی راه‌اندازی می‌شود. برای اینکه یک واحد جانبی به‌طور کامل راه‌اندازی شود باید از یک توالی خاص از چندین توابع \lr{LL} استفاده شود.
	
	\item \textbf{توابع \lr{(Hardware Abstraction Layer)HAL}}: در این نوع توابع که در بالاترین سطح ممکن است، با سطح رجیستر خیلی فاصله‌ وجود دارد و عملاً به‌ندرت از رجیسترها استفاده می‌شود، اگرچه دسترسی به رجییسترها در این سطح بدون هیچ مشکلی ممکن است و با استفاده از ماکروهایی می‌توان به رجیسترها دسترسی داشت. وقتی‌که از یک تابع \lr{HAL} استفاده می‌شود علاوه بر اینکه خودش رجیسترهای یک بخش را تنظیم می‌کند، در اکثر موارد بسیاری از کارهایی که در توابع \lr{LL} باید خود کاربر انجام می‌داد را نیز انجام می‌دهد.
	
	مثلاً اگر قرار بود در توابع \lr{LL}، از 5 تابع استفاده شود و کمی هم توابع زبان \lr{C} به‌کار برده شود تا یک واحد جانبی راه‌اندازی شود، ممکن است تمامی این کارها با یک تابع \lr{HAL} انجام شود.
	\item \textbf{توابع \lr{(Standard peripheral libraries)SPL}}: توابع \lr{SPL} در سطح میانی قرار دارند و می‌توان گفت سطحی بین \lr{LL} و \lr{HAL} را دارا هستند. البته این توابع دیگر به‌روزرسانی نمی‌شوند. بنابراین امروزه به جای این توابع از توابع \lr{HAL} که قابلیت‌های بسیار بهتری دارند، استفاده می‌شود.
	
\end{itemize}

توابع \lr{HAL} به‌قدری همه‌چیز را آماده کرده‌اند که اگر به خوبی بررسی شوند، مشاهده می‌شود که در بعضی موارد اگر کاربر سهواً یا از روی ندانستن اشتباهی انجام داده باشد، آن اشتباه را اگر ممکن باشد و تشخیص بدهد، تصحیح می‌کند. منطقاً هرکدام از این روش‌ها برای هدف خاصی مناسب هستند، و این‌گونه نیست که یک روش کاملاً ناکارآمد و به‌دردنخور باشد. به‌عنوان‌مثال اگر هدف سرعت برنامه باشد، توابع \lr{HAL} اصلاً توصیه نمی‌شوند و رجیستری بهترین انتخاب است. در نقطه‌ی مقابل اگر هدف سرعت توسعه‌ی پروژه باشد و سرعت برنامه مدنظر نباشد، بهترین انتخاب توابع \lr{HAL} هستند و رجیستری اصلاً توصیه نمی‌شود.
\newpage
\subsection{کانفیگ پایه‌های میکروکنترلر}
هر پین میکروکنترلر ممکن است چندین گزینه برای کانفیگ شدن داشته باشد.  برای مثال اگر به دیتاشیت \lr{STMF103C8T6} مراجعه کنید. برای پین \lr{PB6} چندین کارکرد از جمله \lr{USART1-TX} و \lr{I2C1-SCL} و \lr{Timer4-Channel1} وجود دارد که تنها باید یکی از آنها را انتخاب نمود. ما نمی‌توانیم این پایه را هم به عنوان \lr{Tx} واحد \lr{USART1} و هم به عنوان \lr{SCL} پروتکل \lr{I2C} تنظیم کنیم. چراکه این کار باعث به وجود آمدن تداخل می‌شود. از ویژگی‌های مفید \lr{CubeMX} این است که در صورت امکان تداخل در کانفیگ پین‎های میکروکنترلر، این موضوع را به ما نشان می‌دهد و مانع از بروز مشکل می‌شود.

    \begin{figure}[!h]
	\centering
	
	\caption[کانفیگ میکروکنترلر]{کانفیگ میکروکنترلر}
	\label{کانفیگ میکروکنترلر}
	\end{figure}

\subsection{تنظیم کلاک}
به نوعی مشابه ویژگی قبلی، در قسمت تنظیم کلاک نرم‌افزار \lr{CubeMX} امکانی وجود دارد که کمک می‌کند به تنظیم قسمت‌های مختلف کلاک  پرداخته شود. در واقع در اینجا هم اگر مقداری خارج از حد مجاز به قسمتی از کلاک داده شود، با رنگ قرمز وجود مشکل را اعلام می‌کند. در صورت به وجود آمدن این وضعیت، به صورت اتوماتیک (توسط نرم افزار) یا دستی (توسط خودمان) مقادیر به حالت مجاز تغییر داده می‌شوند.

    \begin{figure}[!h]
	\centering
	
	\caption[تنظیم کلاک]{تنظیم کلاک}
	\label{تنظیم کلاک}
	\end{figure}

\vspace{1cm}
\subsection{تنظیمات موردنیاز برای ربات چهارپا}
کلاک داخلی میکروکنترلر 8 مگاهرتز می‌باشد و با استفاده از کریستال خارجی می‌توان به 72 مگاهرتز ارتقا داد، در این پروژه هم برای سرعت بالاتر از کریستال خارجی استفاده شده است و به این دلیل که به سرعت خیلی بالایی نیاز نیست ولی دقت پارامتر مهمی است پس کلاک را روی 36 مگاهرتز تنظیم شده است.

در این پروژه همان‌طورکه قبلا به آن اشاره شده است، به 12 پایه \lr{PWM} نیاز است و در میکروکنترلر مورد استفاده چهار تایمر وجود دارد که هر تایمر دارای 4 کانال می‌باشد پس، از 12 تا از این کانال‌ها استفاده می‌شود. برای درست کار کردن هر تایمر در ابتدا نیاز است که تنظیماتی اعمال شود.

همانطور که در فصل قبل به آن اشاره شد، سروموتور به دامنه زمانی 20 میلی ثانیه یا فرکانس 50 هرتز نیاز دارد. در این نرم‌افزار با دو پارامتر می‌توان به مقدار مطلوب رسید که فرمول به شکل زیر است:
\begin{equation}
	F_{PWM} = \frac{F_{CLK}}{(ARR + 1)*(PSC + 1)}
\end{equation}

پارامترهای \lr{PSC}\unskip\LTRfootnote{Prescale} و \lr{ARR}\unskip\LTRfootnote{Auto Reload Register}(\lr{counter period}) به شکلی انتخاب می‌شوند تا به فرکانس 50 هرتز دست یافته شود. فرکانس کلاک برابر با 36 مگاهرتز است پس مخرج که ضرب دوتا پارامتر می‌باشد باید برابر با 720000 شود؛ حال می‌توان هر مقداری برای این دو پارامتر درنظر گرفت ولی با توجه به چرخه کار مدنظر برای \lr{PSC} مقداری خاص انتخاب می‌شود. 
\begin{equation}
	DutyCycle =\frac{CCR}{ARR}
\end{equation}
نیاز است ابتدا و انتهای بازه برای مقداردهی \lr{PWM} بدست آورده شود که مقداردهی آن به صورت رجیستری است:
\begin{itemize}
	\item \textbf{زاویه 0 درجه}: همانطور که گفته شد بین بازه 5.0 تا 1 میلی ثانیه سیگنال روشن است پس نسبت چرخه کار 5.2 درصد می‌باشد و برای راحتی در محاسبات، \lr{PSC} 999 در نظر گرفته می‌شود، درنهایت مقدار \lr{CCR} 25 بدست می‌آید.
	\item \textbf{زاویه 90 درجه}: برای میانه بازه، نسبت چرخه کار 5.1 به 20 می‌باشد که برابر با 7.5 درصد است و همانطورکه \lr{PSC} 999 قرار داده شده است پس \lr{CCR} باید 75 مقداری دهی شود.
	\item \textbf{زاویه 180 درجه}: در نهایت، برای بیشترین زاویه که 180 درجه می‌باشد، سیگنال به اندازه 2 تا 5.2 میلی ثانیه روشن می‌ماند پس نسبت چرخه کار برابر با 5.12 می‌شود و مقدار انتهایی \lr{CCR} هم 125 می‌باشد. 
\end{itemize}

    \begin{figure}[!h]
	\centering
	
	
	\caption[تنظیمات تایمر]{تنظیمات تایمر}
	\label{تنظیمات تایمر}
	\end{figure}

برای تنظیمات پروتکل \lr{UART} هم در ابتدا باید \lr{Baud Rate} یکسانی برای دو پردازنده انتخاب شود تا با سرعت یکسانی کار کنند که در این پروژه بر روی 115200 بیت بر ثانیه تنظیم شده است. سپس در قسمت انتخاب مد، گزینه آسنکرون انتخاب شده است به این دلیل که به همزمانی نیاز نیست و همچنین حجم داده ارسالی خیلی زیادی وجود ندارد و سرعت انتقال داده این مد مناسب است و به سرعت بالاتری که منجر به استفاده از ارتباط سنکرون شود نیازی نیست.

دو نکته دیگر در کار با ارتباط سریال خیلی مهم هستند؛ زمانی که دوریبین مانعی را تشخیص دهد از طریق سریال به پردازنده اصلی داده‌ای ارسال می‌شود که کدام نوع مانع دیده شده است، چالشی که با آن مواجه شدیم این بود که ما نیاز به ارسال بلادرنگ\LTRfootnote{Real Time} داده است اما در سمت دریافت، داده فقط یکبار دریافت می‌شود پس ما مد گیرنده را روی \lr{Circular} قرار می‌دهیم که در هرلحظه داده را بگیرد.

در نهایت هم برای بهینه شدن کد و عملکرد آن، که در هر لحظه قصد خواندن داده نداشته باشد از وقفه\LTRfootnote{Interrupt} استفاده شده است که باعث می‌شود همان لحظه که داده فرستاده می‌شود، داده را خوانده و آن را ذخیره کند.

    \begin{figure}[!h]
	\centering
	
	
	
	
	\caption[تنظیمات ارتباط سریال]{تنظیمات ارتباط سریال}
	\label{تنظیمات ارتباط سریال}
	\end{figure}

\section{برنامه‌نویسی در نرم‌افزار \lr{Keil}}
\subsection{نرم‌افزار \lr{Keil} چیست؟}
نرم افزار \lr{Keil} یا \lr{Keil MDK} یا \lr{MDK} (مخفف \lr{Microcontroller Development Kit}) که ساخت شرکت \lr{Keil} است، برای توسعۀ طیف وسیعی از میکروکنترلرهای \lr{ARM Cortex-M } و میکروکنترلرهای دیگر است. این نرم افزار شامل یک \lr{IDE} است که \lr{µVision IDE} نام دارد. همچنین شامل محیط ویرایشگر کد، پروگرامر و دیباگر، شبیه ساز، کامپایلر و \lr{…} است و این امکان را به کاربر می دهد که به راحتی بتواند برای میکروکنترلرها برنامه نویسی کند.

در ابتدا تنظیمات موردنیاز را در \lr{Cube MX} انجام می‌دهیم و برای ما در \lr{Keil} کد خام تولید می‌کند تا دیگر نیاز نباشد تمام کد را از ابتدا بنویسیم.
\subsection{تنظیم تایمرها}
ما در ربات 12 عدد موتور داریم که هر موتور با \lr{PWM} کار می‌کند پس نیاز به 12 پایه تایمر داریم. همانطور که در قسمت‌های قبل به آن شاره شد در این میکروکنترلر 4 عدد تایمر داریم که هر تایمر هم 4 عدد کانال دارد پس در کل 16 پایه با این قابلیت موجود است. به این دلیل که هر پایه در این میکروکنترلر چندین قابلیت دارد باید حتما به آن دستور داده شود که از کدام قبلیت می‌خواهیم استفاده کنیم تا تصادفاً مشکلی پیش نیاید. هیچ تفاوتی وجود ندارد که از کدام 16 پایه استفاده کنیم؛ فقط دو تا از پایه‌ها برای ارتباط سریال استفاده می‌شوند پس انتخاب از 14 پایه دیگر است.
\begin{latin}
	\lstinputlisting[style=c_style]{code/Timer_Initialize.c}
\end{latin}
\subsection{تابع حرکت موتور}
در مرحله بعدی که تایمر را فعالسازی کردیم، توابع حرکت موتورها را می‌نویسیم. برای حرکت دادن هر موتور نیاز داریم که به صورت رجیستری به آن دستور بدهیم و همانطور که قبلاً به آن اشاره کردیم، مجاز هستیم در بازه 25 تا 125 فرمان بدهیم. برای انجام اینکار نیاز داریم که شماره تایمر، کانال و مقدار \lr{PWM} را بدانیم. نکته مهم آن است که ما مقدار در لحظه هر موتور را در یک آرایه ذخیره می‌کنیم و این تابع دستور می‌دهیم که از زاویه قبلی به زاویه جدید و دلخواه برود. 
\begin{latin}
	\lstinputlisting[style=c_style]{code/Move.c}
\end{latin}
نوعی دیگر از حرکت که برای موتورها درنظر گرفتیم، حرکت چهارپا همزمان است. به این صورت که چهارپای اول، دوم یا سوم به صورت همزمان حرکت می‌‌کنند که برای بلند شدن ربات استفاده می‌شود چون اگر هر پا مجزا حرکت بکنند ربات تعادل نخواهد داشت و ربات به یک سمت می‌افتد.
\begin{latin}
	\lstinputlisting[style=c_style]{code/Move_All_Motors.c}
\end{latin}
\subsection{چهار حرکت اصلی ربات}
بعد از آنکه تمام حرکت‌ها را نوشتیم و بدست آوردیم شروع به نوشتن چهار حرکت اصلی می‌کنیم اما قبل از آن باید دستوری به ربات بدهیم که در ابتدا که شروع به حرکت می‌کند، به یک نقطه یا حالت اولیه برود که تعادل داشته باشد و به راحتی بدون لغزش بایستد.

در این تابع ابتدا به چهار موتور اول هر پا سپس چهار موتور دوم و در انتها هم به چهار موتور سوم دستور می‌دهیم که به زاویه مطلوب برود. به اینصورت عمل می‌کند که تمام چهار موتور با یکدیگر حرکت می‌کنند و برای اینکار تابع \lr{Move All} را فراخوانی می‌کنیم.

\begin{latin}
	\lstinputlisting[style=c_style]{code/Home.c}
\end{latin}

حرکت بعدی که آن را پیاده سازی کردیم، حرکت به سمت جلو می‌باشد که ربات با کمک اصطکاک و لغزش به سمت جلو حرکت می‌کند. در این حرکت ابتدا یکی از دو پای جلو باز شده تا مرکز ثقل به آن سمت برود و در این حالت پای مقابل آن در عقب ربات می‌تواند از زمین بلند شود و به سمت جلو برود و سپس پای جلو ربات که باز شده بود به حالت قبلی برمی‌گردد اما پای عقب جلو تر از حالت اولیه و صفر خود است پس وقتی به حالت قبلی برمی‌گردد، ربات به کمک اصطکاک پا به جلو حرکت می‌کند.

\begin{latin}
	\lstinputlisting[style=c_style]{code/Forward.c}
\end{latin}

حرکت به سمت عقب رفتن هم به همین شکل است فقط پاهای جلو و عقب عکس جلو رفتن عمل می‌کنند. ابتدا پای عقب باز شده و سپس پای مقابل آن در جلو ربات ابتدا از زمین بلند شده و به سمت عقب حرکت می‌کند؛ سپس پای عقب به حالت اولیه باز می‌گردد و پای جلو که به زمین رسیده است به سمت جلو حرکت می‌کند و با اصطکاک ایجاد شده ربات به سمت عقب می‌رود.

\begin{latin}
	\lstinputlisting[style=c_style]{code/Backward.c}
\end{latin}

در نهایت هم چرخش به سمت چپ و راست را داریم که به این صورت است که برای چرخش به چپ پای عقب راست باز شده تا پای جلو چپ از زمین جدا شده به سمت عقب حرکت کند و سپس بسته شده تا پای جلو چپ به زمین برسد؛ بعد از آن همان پا بسته می‌شود تا پای عقب راست از زمین جدا شده و جلو برود. در نهایت با برگشتن پای جلو چپ به حالت قبلی، دو پا همزمان به حالت اولیه حرکت می‌کنند و ربات به سمت چپ می‌چرخد.

\begin{latin}
	\lstinputlisting[style=c_style]{code/Turn_Left.c}
\end{latin}

\vspace{1cm}
برای چرخش به راست هم به همین شکل فقط به جای پای عقب راست و جلو چپ، پای عقب چپ و جلو راست را داریم.

\begin{latin}
	\lstinputlisting[style=c_style]{code/Turn_Right.c}
\end{latin}

\subsection{عملکرد کلی ربات}
با همه نکاتی که گفتیم و توابعی که نوشتیم باید از آن‌‌ها استفاده کنیم به شکلی که ربات به سمت هدف حرکت کرده و از موانع دور شود. پس با استفاده از دوربین و تشخیص رنگ یک کاراکتر از طریق ارتباط سریال دریافت می‌کنیم و نسبت به رنگی که دارد دستور می‌دهیم که چه کاری انجام شود. ما کنار کاراکتر رنگ یک عدد سه رقمی از مساحت مانع هم می‌گیریم که هرچه به مانع نزدیکتر شویم این عدد بزرگتر شده پس می‌دانیم کی باید حرکت دیگری انجام دهیم که برخورد نداشته باشیم.

\begin{latin}
	\lstinputlisting[style=c_style]{code/Main.c}
\end{latin}

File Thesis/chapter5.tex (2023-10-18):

\chapter{نتيجه‌گيري و پیشنهادات}

\section{نتيجه‌گيري}
در فصول پیشین با توجه به مزیت‌های ذکر شده برای ربات چهارپا و مشخصات مطلوب مدنظر، مدل نهایی طراحی شد. با انجام اصلاحاتی روی ربات، قطعات جدید پرینت شد و مدل نهایی در عمل پیاده سازی شد. در قسمت سخت‌افزار ربات، با توجه اینکه سروموتور \lr{SG90} نیاز ما را از لحاظ سبکی و گشتاور لازم برای بلند کردن و حرکت ربات و مقرون به صرفه بودن برطرف نمود از آن استفاده شد، همچنین کم بودن پایه‌های \lr{Arduino Uno} برای استفاده از \lr{PWM} منجر به استفاده از میکروکنترلر \lr{STM32F103C8T6} شد. برای تشخیص موانع موجود به دلیل قیمت مناسب، موجود در بازار و کیفیت مطلوب ماژول \lr{ESP32-CAM} به کار برده شد. به این دلیل که وزنی به ربات اضافه نشود به جای آنکه باتری بر روی ربات قرار بگیرد و موتورها را برای حرکت دادن ربات دچار مشکل کند، از منبع ولتاژ \lr{DC} استفاده شد و همچنین 12 موتور در بعضی مواقع مانند بلند شدن ربات از زمین، جریانی زیادی را می‌کشند که ممکن است باتری نتواند آن را تامین کند.
	\begin{figure}[!h]
	\centering
	
	\caption{ربات نهایی}
	\end{figure}
	
\newpage
برای قسمت نرم‌افزار ربات، برای برقراری ارتباط بین میکروکنترلر و دوربین، از پروتکل \lr{UART} استفاده شد. برای حفظ تعادل و حرکت در مسیر درست، نیاز است که هر موتور دقیقاً به موقعیت مطلوب برود پس برای کنترل موقعیت و زاویه هر موتور تکنیک کنترلی \lr{PWM} به کار برده شد. برای انجام تنظیمات مورد نیاز میکروکنترلر و به جهت ساده‌تر کردن و سرعت بخشیدن به برنامه‌نویسی میکروکنترلر از نرم‌افزار \lr{CubeMX} بهره برده شد. درنهایت به دلیل رایج بودن محیط برنامه‌نویسی \lr{Keil}، برای فعال‌سازی و راه‌اندازی تایمرها و نوشتن توابع حرکتی ربات از آن استفاده شد.
	\begin{figure}[!h]
	\centering
	
	\caption{ربات نهایی}
	\end{figure}
	
\newpage
برای جابه‌جایی ربات از نقطه‌ای به نقطه دیگر از اصطکاک پاها کمک گرفته شده است و در تمام حرکت‌های ربات اعم از حرکت رو به جلو و عقب، به موتورها فرمانی داده شده است که با استفاده از اصطکاک و عکس العمل آن ربات به سمت دلخواه حرکت کند. همچنین برای بلند شدن ربات و قرارگیری در حالت اولیه، به موتورهای اول، دوم یا سوم هر پا همزمان فرمان داده می‌شود تا ربات در هنگام بلند شدن تعادل خود را نگه دارد و بدون لعزش بایستد. در شکل \ref{State0} ربات بدون هیچ دستور و ولتاژی به موتورهایش روی زمین قرار گرفته است اما با اعمال ولتاژ به موتورها و میکروکنترلر، دستور رفتن به حالت اولیه (\ref{State1}) اتفاق می‌افتد.
    \begin{figure}[!h]
	\centering
	
	\caption{ربات بدون هیچ فرمان}
	\label{State0}
	\end{figure}
	\begin{figure}[!h]
	\centering
	
	\caption{ربات در حالت اولیه}
	\label{State1}
	\end{figure}
	
\section{پیشنهادات}
با توجه به تجربیاتی که از ساخت ربات بدست آوردیم، بهتر است از سروموتورهای قوی‌تر و بهتری استفاده شود که در حرکت دادن پاهای ربات مشکلی وجود نداشته باشد و همچنین بهتر است پای دوم کوتاه‌تر از پای سوم باشد و به شکلی ربات قرار بگیرد که در حالت اولیه ربات که ربات ایستاده است؛ بدنه از مفصل پای سوم پایینتر باشد و به زمین نزدیک باشد. مهمترین نکته هم آن است که چرخ‌دنده‌های موتورها پلاستیکی نباشد چون با کوچکترین فشاری از خارج به ربات باعث شکستن چرخ‌دنده می‌شود.

اگر از سروموتور قوی‌تری استفاده شود، می‌توان بدنه را کمی سبکتر ساخت و دیگر نیازی به منبع ولتاژ ثابت نباشد و به جای آن از باتری استفاده گردد که جابه‌جایی ربات آسان‌تر انجام شود چون وجود دو سیم منبع ولتاژ می‌تواند مانع انجام درست جرکت‌ها شود (فقط به این توجه شود که باتری توان جریان‌کشی زیاد موتورها را داشته باشد).

به جای حرکت به کمک اصطکاک بهتر است که طراحی به شکلی صورت گیرد که ربات قادر به گام‌برداری باشد به صورتی که اگر یک پا از زمین جدا شود و به سمتی حرکت کند ربات تعادل داشته باشد و واژگون نشود. به این ترتیب ربات وابستگی به جنس محیط برای داشتن اصطکاک مطلوب ندارد.

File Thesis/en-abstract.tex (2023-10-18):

%کلمات کلیدی انگلیسی
\latinkeywords{Mobie Robots, Quadrupedal Robot, Legged Robot, SolidWorks, Algorithm, Microcontroller}
%چکیده انگلیسی

\en-abstract{
In today's world, robots play a significant role in human life. Mobile robots, due to their interaction with the environment, differ from other machines. They can create changes in their surroundings based on their actions and respond to the world around them. The diverse applications of robots in simplifying human life have led engineers to pay special attention to robots.
\\
Among all mobile robots, quadruped robots are a type of legged robot that, due to their ability to explore all types of terrains like humans and animals, outperform wheeled robots. The advantage of quadruped robots is that they maintain their stability when standing still and require control when walking.
\\
In this thesis, we first introduced robots, their types, with a focus on constructed quadruped robots, and their applications. Then, we delved into the discussion of designing a model and building a robot using SolidWorks software. In this design process, an initial model was created, and efforts were made to improve its performance after addressing its flaws, resulting in a refined final version. Subsequently, we discussed the hardware and components used in the robot, including motors, microcontrollers, and various modules. Finally, we described the algorithms used and the programming on the robot's microcontroller. 
}
%%%%%%%%%%%%%%%%%%%%% کدهای زیر را تغییر ندهید.

\newpage
\thispagestyle{empty}
\begin{latin}
	\begin{flushleft}
	\section*{\LARGE\centering Abstract}

	\een-abstract

	\vspace*{.5cm}
	{\large\textbf{Key Words:}}\par
	\vspace*{.5cm}
	\elatinkeywords
	\end{flushleft}
\end{latin}

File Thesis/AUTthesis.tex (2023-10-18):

%%%  کلاس AUTthesis، نسخه آبان 1397
%%%   دانشگاه صنعتی امیرکبیر                 http://www.aut.ac.ir
%%%  تالار گفتگوی پارسی‌لاتک،       http://forum.parsilatex.com
%%%   آپدیت شده در آبان 95
%%%   پشتیبانی و راهنمایی          badali_farhad@yahoo.com
%%%
%%%   بازبینی و اصلاح شده در آبان ماه 1397
%%%  Tested via TeXstudio in TeXlive 2014-2018.
%%%

%-----------------------------------------------------------------------------------------------------
%        روش اجرا.: 2 بار F1 ، 2 بار  F11(به منظور تولید مراجع) ، دوبار Ctrl+Alt+I (به منظور تولید نمایه) و دو بار F1 -------> مشاهده Pdf
%%%%%%%%%%%%%%%%%%%%%%%%%%%%%%%%%%%%%%%%%%%%%%%%%%%%%%
%   TeXstudio as your IDE
%%  برای compile در TeXstudio تنها کافی است منوی Options->Configure TeXstudio را زده و در پنجره Configure TeXstudio در بخش Build گزینه Default Compiler را به XeLaTeX تغییر دهید. سند شما به راحتی compile خواهد شد.
%   F1 & F5 : Build & view
%   F6      : Compile
%   F7      : View
%   --------------
%%%%%%%%%%%%%%%%%%%%%%%%%%%%%%%%%%%%%%%%%%%%%%%%%%%%%%
%        اگر قصد نوشتن رساله دکتری را دارید، در خط زیر به جای msc،
%      کلمه phd را قرار دهید. کلیه تنظیمات لازم، به طور خودکار، اعمال می‌شود.
%%% !TEX TS-program = XeLaTeX
\documentclass[oneside,bsc,12pt]{AUTthesis}
%       فایل commands.tex را حتماً به دقت مطالعه کنید؛ چون دستورات مربوط به فراخوانی بسته زی‌پرشین 
%       و دیگر بسته‌ها و ... در این فایل قرار دارد و بهتر است که با نحوه استفاده از آنها آشنا شوید. توجه شود برای نسخه نهایی پایان‌نامه حتماً hyperref را 
%        غیرفعال کنید.

\input{commands}

\begin{document}
	\baselineskip=.75cm
	\linespread{1.75}
	\input{fa_title}
	% تاییدیه دفاع
	\input{taid}
	% چنانچه مایل به چاپ صفحات «تقدیم»، «نیایش» و «سپاس‌گزاری» در خروجی نیستید، خط‌های زیر را با گذاشتن ٪  در ابتدای آنها غیرفعال کنید.
	% پایان‌نامه خود را تقدیم کنید
	% نیایش خود را در فایل زیر بنویسید.
	%\input{Chant}
	% سپاسگزاری را در فایل زیر بنویسید.
	\input{acknowledgement}
	% دستور زیر برای شماره گذاری صفحات قبل از فصل اول با حروف ابجد است.
	\pagenumbering{alph}
	%-----------------------------------------------------------------------------
	% فایل زیر دستورات مربوط به نمایش صفحات فهرست مطالب- فهرست اشکال و جداول است.
	\input{TOC-TOF-LOT}
	% در صورت تمایل می‌توانید با فعال کردن دستور بالا، لیست تصاویر را به  پایان‌نامه خود اضافه کنید.
	%-------------------------------------------------------------------------symbols(فهرست نمادها)
	% وجود لیست نمادها الزامیست.(لطفاً نمادهای خود را جایگذین نمادهای پیش‌فرض کنید.)
	\input{list-of-symbols}
	
	\pagenumbering{arabic}
	\pagestyle{style1}
	%--------------------------------------------------------------------------chapters(فصل ها)
	\include{chapter1}
	\include{chapter2}
	\include{chapter3}
	\include{chapter4}
	\include{chapter5}
	
	%--------------------------------------------------------------------------appendix( مراجع و پیوست ها)
	\chapterfont{\vspace*{-2em}\centering\LARGE}%
	
	\appendix
	\renewcommand{\bibname}{منابع و مراجع}
	\bibliographystyle{plain-fa}
	\bibliography{references}
	\include{appendix1}
	%--------------------------------------------------------------------------dictionary(واژه نامه ها)
	%اگر مایل به داشتن صفحه واژه‌نامه نیستید، خط زیر را غیر فعال کنید.
	%\parindent=0pt
	%\include{dicfa2en}%
	%\include{dicen2fa}
	%--------------------------------------------------------------------------index(نمایه)
	%اگر مایل به داشتن صفحه نمایه نیستید، خط زیر را غیر فعال کنید.
	\pagestyle{style7}
	\printindex
	\pagestyle{style7}
	\include{en-abstract}
	\input{en_title}	
\end{document}

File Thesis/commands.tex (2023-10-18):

% در این فایل، دستورها و تنظیمات مورد نیاز، آورده شده است.
%-------------------------------------------------------------------------------------------------------------------
% در ورژن جدید زی‌پرشین برای تایپ متن‌های ریاضی، این سه بسته، حتماً باید فراخوانی شود.

\usepackage{titlesec}
\setcounter{secnumdepth}{4}
\usepackage{amsthm,amssymb,amsmath,amsfonts}
%Taghire footnote safe be safe
\usepackage{zref-perpage}
\zmakeperpage{footnote}

%این دستور برای فعالسازی سودوکد می‌باشد
\usepackage{listings}
\usepackage{color}

\lstdefinestyle{c_style}{
	belowcaptionskip=1\baselineskip,
	breaklines=true,
	frame=L,
	xleftmargin=\parindent,
	language=c,
	showstringspaces=false,
	basicstyle=\footnotesize\ttfamily,
	keywordstyle=\bfseries\color{blue},
	commentstyle=\itshape\color{mygreen},
	identifierstyle=\color{black},
	stringstyle=\color{purple},
}
\definecolor{mygreen}{rgb}{0,0.6,0}

% بسته‌ای برای تنطیم حاشیه‌های بالا، پایین، چپ و راست صفحه
\usepackage[top=30mm, bottom=30mm, left=25mm, right=30mm]{geometry}
% بسته‌‌ای برای ظاهر شدن شکل‌ها و تصاویر متن
\usepackage{graphicx}
\usepackage{color}
%بسته‌ای برای تنظیم فاصله عمودی خط‌های متن
\usepackage{setspace}
\usepackage{titletoc}
\usepackage{tocloft}
%با فعال کردن بسته زیر فوت‌نوت‌ها در هر صفحه ریست می‌شوند. حالت پیش‌فرض آن ریست شدن در هر فصل می‌باشد.
%\usepackage[perpage]{footmisc}
\usepackage{enumitem}
%\usepackage{titlesec}
% بسته‌ و دستوراتی برای ایجاد لینک‌های رنگی با امکان جهش
\usepackage[pagebackref=false,colorlinks,linkcolor=black,citecolor=blue,urlcolor=blue]{hyperref}
\usepackage[nameinlink]{cleveref}%capitalize,,noabbrev
\AtBeginDocument{%
	\crefname{equation}{برابری}{equations}%
	\crefname{chapter}{فصل}{chapters}%
	\crefname{section}{بخش}{sections}%
	\crefname{appendix}{پیوست}{appendices}%
	\crefname{enumi}{مورد}{items}%
	\crefname{footnote}{زیرنویس}{footnotes}%
	\crefname{figure}{شکل}{figures}%
	\crefname{table}{جدول}{tables}%
	\crefname{theorem}{قضیه}{theorems}%
	\crefname{lemma}{لم}{lemmas}%
	\crefname{corollary}{نتیجه}{corollaries}%
	\crefname{proposition}{گزاره}{propositions}%
	\crefname{definition}{تعریف}{definitions}%
	\crefname{result}{نتیجه}{results}%
	\crefname{example}{مثال}{examples}%
	\crefname{remark}{نکته}{remarks}%
	\crefname{note}{یادداشت}{notes}%
}
% چنانچه قصد پرینت گرفتن نوشته خود را دارید، خط بالا را غیرفعال و  از دستور زیر استفاده کنید چون در صورت استفاده از دستور زیر‌‌، 
% لینک‌ها به رنگ سیاه ظاهر خواهند شد که برای پرینت گرفتن، مناسب‌تر است
%\usepackage[pagebackref=false]{hyperref}
% بسته‌ لازم برای تنظیم سربرگ‌ها
\usepackage{fancyhdr}
% بسته‌ای برای ظاهر شدن «مراجع»  در فهرست مطالب
\usepackage[nottoc]{tocbibind}
% دستورات مربوط به ایجاد نمایه
\usepackage{makeidx,multicol}
\setlength{\columnsep}{1.5cm}

%%%%%%%%%%%%%%%%%%%%%%%%%%
\usepackage{verbatim}
\makeindex
\usepackage{sectsty}
% فراخوانی بسته زی‌پرشین و تعریف قلم فارسی و انگلیسی
\usepackage{xepersian}%[extrafootnotefeatures]
\SepMark{-}
%حتماً از تک لایو 2014 استفاده کنید.
\settextfont[Scale=1.2]{B Nazanin}
\setlatintextfont{Times New Roman}
\renewcommand{\labelitemi}{$\bullet$}
%%%%%%%%%%%%%%%%%%%%%%%%%%
% چنانچه می‌خواهید اعداد در فرمول‌ها، انگلیسی باشد، خط زیر را غیرفعال کنید.
%در غیر اینصورت حتماً فونت PGaramond را نصب کنید.
%\setdigitfont[Scale=1.1]{PGaramond}%%Yas
%%%%%%%%%%%%%%%%%%%%%%%%%%
% تعریف قلم‌های فارسی اضافی برای استفاده در بعضی از قسمت‌های متن
\defpersianfont\nastaliq[Scale=2]{IranNastaliq}
\defpersianfont\chapternumber[Scale=3]{B Nazanin}
%\chapterfont{\centering}%
%%%%%%%%%%%%%%%%%%%%%%%%%%
% دستوری برای تغییر نام کلمه «اثبات» به «برهان»
\renewcommand\proofname{\textbf{برهان}}

% دستوری برای تغییر نام کلمه «کتاب‌نامه» به «منابع و مراجع«
\renewcommand{\bibname}{منابع و مراجع}

% Headings for every page of ToC, LoF and Lot
\setlength{\cftbeforetoctitleskip}{-1.2em}
\setlength{\cftbeforelottitleskip}{-1.2em}
\setlength{\cftbeforeloftitleskip}{-1.2em}
\setlength{\cftaftertoctitleskip}{-1em}
\setlength{\cftafterlottitleskip}{-1em}
\setlength{\cftafterloftitleskip}{-1em}
%%\makeatletter
%%%%\renewcommand{\l@chapter}{\@dottedtocline{1}{1em\bfseries}{1em}}
%%%%\renewcommand{\l@section}{\@dottedtocline{2}{2em}{2em}}
%%%%\renewcommand{\l@subsection}{\@dottedtocline{3}{3em}{3em}}
%%%%\renewcommand{\l@subsubsection}{\@dottedtocline{4}{4em}{4em}}
%%%%\makeatother

\newcommand\tocheading{\par عنوان\hfill صفحه \par}
\newcommand\lofheading{\hspace*{.5cm}\figurename\hfill صفحه \par}
\newcommand\lotheading{\hspace*{.5cm}\tablename\hfill صفحه \par}

\renewcommand{\cftchapleader}{\cftdotfill{\cftdotsep}}
\renewcommand{\cfttoctitlefont}{\hspace*{\fill}\LARGE\bfseries}%\Large
\renewcommand{\cftaftertoctitle}{\hspace*{\fill}}
\renewcommand{\cftlottitlefont}{\hspace*{\fill}\LARGE\bfseries}%\Large
\renewcommand{\cftafterlottitle}{\hspace*{\fill}}
\renewcommand{\cftloftitlefont}{\hspace*{\fill}\LARGE\bfseries}
\renewcommand{\cftafterloftitle}{\hspace*{\fill}}

%%%%%%%%%%%%%%%%%%%%%%%%%%
% تعریف و نحوه ظاهر شدن عنوان قضیه‌ها، تعریف‌ها، مثال‌ها و ...
%برای شماره گذاری سه تایی قضیه ها
\theoremstyle{definition}
\newtheorem{definition}{تعریف}[section]
\newtheorem{remark}[definition]{نکته}
\newtheorem{note}[definition]{یادداشت}
\newtheorem{example}[definition]{نمونه}
\newtheorem{question}[definition]{سوال}
\newtheorem{remember}[definition]{یاداوری}
\theoremstyle{theorem}
\newtheorem{theorem}[definition]{قضیه}
\newtheorem{lemma}[definition]{لم}
\newtheorem{proposition}[definition]{گزاره}
\newtheorem{corollary}[definition]{نتیجه}
%%%%%%%%%%%%%%%%%%%%%%%%
%%%%%%%%%%%%%%%%%%%
%%% برای شماره گذاری چهارتایی قضیه ها و ...
%%\newtheorem{definition1}[subsubsection]{تعریف}
%%\newtheorem{theorem1}[subsubsection]{قضیه}
%%\newtheorem{lemma1}[subsubsection]{لم}
%%\newtheorem{proposition1}[subsubsection]{گزاره}
%%\newtheorem{corollary1}[subsubsection]{نتیجه}
%%\newtheorem{remark1}[subsubsection]{نکته}
%%\newtheorem{example1}[subsubsection]{مثال}
%%\newtheorem{question1}[subsubsection]{سوال}

%%%%%%%%%%%%%%%%%%%%%%%%%%%%

% دستورهایی برای سفارشی کردن صفحات اول فصل‌ها
\makeatletter
\newcommand\mycustomraggedright{%
	\if@RTL\raggedleft%
	\else\raggedright%
	\fi}
\def\@makechapterhead#1{%
	\thispagestyle{style1}
	\vspace*{20\p@}%
	{\parindent \z@ \mycustomraggedright
		\ifnum \c@secnumdepth >\m@ne
		\if@mainmatter
		
		\bfseries{\Huge \@chapapp}\small\space {\chapternumber\thechapter}
		\par\nobreak
		\vskip 0\p@
		\fi
		\fi
		\interlinepenalty\@M 
		\Huge \bfseries #1\par\nobreak
		\vskip 120\p@
		
	}
	
	%\thispagestyle{empty}
	\newpage}
\bidi@patchcmd{\@makechapterhead}{\thechapter}{\tartibi{chapter}}{}{}
\bidi@patchcmd{\chaptermark}{\thechapter}{\tartibi{chapter}}{}{}
\makeatother

\pagestyle{fancy}
\renewcommand{\chaptermark}[1]{\markboth{\chaptername~\tartibi{chapter}: #1}{}}

\fancypagestyle{style1}{
	\fancyhf{} 
	\fancyfoot[c]{\thepage}
	\fancyhead[R]{\leftmark}%
	\renewcommand{\headrulewidth}{1.2pt}
}

\fancypagestyle{style2}{
	\fancyhf{}
	\fancyhead[R]{چکیده}
	\fancyfoot[C]{\thepage{}}
	\renewcommand{\headrulewidth}{1.2pt}
}

\fancypagestyle{style3}{%
	\fancyhf{}%
	\fancyhead[R]{فهرست نمادها}
	\fancyfoot[C]{\thepage}%
	\renewcommand{\headrulewidth}{1.2pt}%
}

\fancypagestyle{style4}{%
	\fancyhf{}%
	\fancyhead[R]{فهرست جداول}
	\fancyfoot[C]{\thepage}%
	\renewcommand{\headrulewidth}{1.2pt}%
}

\fancypagestyle{style5}{%
	\fancyhf{}%
	\fancyhead[R]{فهرست اشکال}
	\fancyfoot[C]{\thepage}%
	\renewcommand{\headrulewidth}{1.2pt}%
}

\fancypagestyle{style6}{%
	\fancyhf{}%
	\fancyhead[R]{فهرست مطالب}
	\fancyfoot[C]{\thepage}%
	\renewcommand{\headrulewidth}{1.2pt}%
}

\fancypagestyle{style7}{%
	\fancyhf{}%
	\fancyhead[R]{نمایه}
	\fancyfoot[C]{\thepage}%
	\renewcommand{\headrulewidth}{1.2pt}%
}

\fancypagestyle{style8}{%
	\fancyhf{}%
	\fancyhead[R]{منابع و مراجع}
	\fancyfoot[C]{\thepage}%
	\renewcommand{\headrulewidth}{1.2pt}%
}
\fancypagestyle{style9}{%
	\fancyhf{}%
	\fancyhead[R]{واژه‌نامه‌ی فارسی به انگلیسی}
	\fancyfoot[C]{\thepage}%
	\renewcommand{\headrulewidth}{1.2pt}%
}
%

%دستور حذف نام لیست تصاویر و لیست جداول از فهرست مطالب
\newcommand*{\BeginNoToc}{%
	\addtocontents{toc}{%
		\edef\protect\SavedTocDepth{\protect\the\protect\value{tocdepth}}%
	}%
	\addtocontents{toc}{%
		\protect\setcounter{tocdepth}{-10}%
	}%
}
\newcommand*{\EndNoToc}{%
	\addtocontents{toc}{%
		\protect\setcounter{tocdepth}{\protect\SavedTocDepth}%
	}%
}
\newcounter{savepage}
\renewcommand{\listfigurename}{فهرست اشکال}
\renewcommand{\listtablename}{فهرست جداول}
%\renewcommand\cftsecleader{\cftdotfill{\cftdotsep}}
%%%%%%%%%%%%%%%%%%%%%%%%%%%%%
%%%%%%%%%%%%%%%%%%%%%%%%%%%%

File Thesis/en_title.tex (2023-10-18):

% در این فایل، عنوان پایان‌نامه، مشخصات خود و چکیده پایان‌نامه را به انگلیسی، وارد کنید.
%%%%%%%%%%%%%%%%%%%%%%%%%%%%%%%%%%%%
\baselineskip=.6cm
\begin{latin}

\latinfaculty{Electrical Engineering Department}

\latintitle{Design and Manufacture of Four-Legged Robot}

\firstlatinsupervisor{Dr. Mohammad Azam Khosravi}

\firstlatinadvisor{Dr. Masoud Shafiee}

\latinname{Mohammad}

\latinsurname{Barabadi}

\latinthesisdate{September 2023}

\latinvtitle
\end{latin}

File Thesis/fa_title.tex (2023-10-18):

%% -!TEX root = AUTthesis.tex
% در این فایل، عنوان پایان‌نامه، مشخصات خود، متن تقدیمی‌، ستایش، سپاس‌گزاری و چکیده پایان‌نامه را به فارسی، وارد کنید.
% توجه داشته باشید که جدول حاوی مشخصات پروژه/پایان‌نامه/رساله و همچنین، مشخصات داخل آن، به طور خودکار، درج می‌شود.
%%%%%%%%%%%%%%%%%%%%%%%%%%%%%%%%%%%%
% دانشکده، آموزشکده و یا پژوهشکده  خود را وارد کنید
\faculty{دانشکده مهندسی برق}
% گرایش و گروه آموزشی خود را وارد کنید
\department{گرایش کنترل}
% عنوان پایان‌نامه را وارد کنید
\fatitle{طراحی و ساخت ربات چهارپا
	\\[.75 cm]}
% نام استاد(ان) راهنما را وارد کنید
\firstsupervisor{دکتر محمد اعظم خسروی}
%\secondsupervisor{استاد راهنمای دوم}
% نام استاد(دان) مشاور را وارد کنید. چنانچه استاد مشاور ندارید، دستور پایین را غیرفعال کنید.
%\firstadvisor{نام کامل استاد مشاور}
%\secondadvisor{استاد مشاور دوم}
% نام نویسنده را وارد کنید
\name{محمد }
% نام خانوادگی نویسنده را وارد کنید
\surname{برآبادی}
%%%%%%%%%%%%%%%%%%%%%%%%%%%%%%%%%%
\thesisdate{شهریور 1402}

% چکیده پایان‌نامه را وارد کنید
\fa-abstract{
امروزه ربات‌ها نقش به‌سزایی در زندگی انسان ها دارند. ربات‌های متحرک به دلیل نحوه تعامل‌شان با جهان، با سایر ماشین‌ها متفاوت هستند. آنها می‌توانند بر اساس اعمال خودشان تغییراتی در محیط اطراف خود ایجاد کنند و به دنیای اطراف خود پاسخ دهند. کاربردهای متنوع ربات ها در راستای ساده‌تر کردن زندگی انسان‌ها باعث شده مهندسین توجه ویژه‌ای به ربات‌ها داشته باشند.
\\
از میان تمامی ربات‌های متحرک، ربات‌های چهارپا یک نوع ربات پادار هستند که به دلیل توانایی آن‌ها برای اکتشاف در همه انواع زمین‌ها، مشابه انسان و حیوانات، نسبت به ربات‌های چرخدار برتری دارند. مزیت ربات‌های چهارپا در این است که هنگام ایستادن نیز حالت پایدار خود را حفظ نموده، اما در هنگام راه رفتن احتیاج به کنترل کردن دارند. 
\\
در این پایان‌نامه، ابتدا با ربات‌ها و انواع آنها با تاکید بر ربات‌های چهارپای ساخته شده و کاربردشان آشنا شده و در ادامه وارد بحث طراحی مدل و ساخت ربات با استفاده از نرم‌افزار سالیدورکس شده‌ایم. در راستای این طراحی، یک مدل اولیه ایجاد شده و پس از رفع عیوب ربات، تلاش بر آن شد که عملکرد آن بهبود یابد و یک نمونه نهایی اصلاح شده پرینت شد. سپس به مبحث سخت‌افزار و قطعات استفاده شده مانند موتور، میکروکنترلر و ماژول‌های مختلف در ربات پرداخته شده است. در پایان نیز الگوریتم‌های استفاده شده و برنامه‌نویسی روی میکروکنترلر ربات شرح داده شده‌اند. 
}

% کلمات کلیدی پایان‌نامه را وارد کنید
\keywords{ربات متحرک\LTRfootnote{Mobile Robot}، ربات چهارپا\LTRfootnote{Quadrupedal Robot}، ربات پادار\LTRfootnote{Legged Robot}، سالیدورکس\LTRfootnote{SolidWorks}، الگوریتم}

\AUTtitle
%%%%%%%%%%%%%%%%%%%%%%%%%%%%%%%%%%
\vspace*{7cm}
\thispagestyle{empty}
\begin{center}
	
\end{center}

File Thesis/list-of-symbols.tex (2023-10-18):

%%%%%%%%%%%%%

{\centering\LARGE\textbf{فهرست نمادها}\par}%

\pagenumbering{alph}
\setcounter{page}{\thesavepage}
%\setcounter{page}{6}
\vspace*{1cm}

\pagestyle{style3}
%\thispagestyle{empty}
%\addcontentsline{toc}{chapter}{فهرست نمادها}
\symb{\text{ نماد}}{مفهوم}
\\
%مقادیر بالا را تغییر ندهید
%%%%%%%%%%%%%%%%%%%%%%%%%%%%%%%%%%%%%%%%%%%%%%%%%%%%%%%%%
\symb{C++}{
نوعی زبان برنامه‌نویسی 
}
\symb{C}{
نوعی زبان برنامه‌نویسی 
}
\symb{mm}{
میلی‌متر 
}
\symb{cm}{
سانتی‌متر 
}
\symb{PB}{
پورت \lr{B}
}
\symb{CLK}{
کلاک 
}
%%%%%%%%%%%%%%%%%%%%%%%%%%%%%%%%%%%%%%%

\thispagestyle{style3}
\newpage
%\pagestyle{style1}
%%%%%%%%%%%%%%%%%%%%%%%%%%%%%%%%%%%%

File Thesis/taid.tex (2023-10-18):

\newpage
\thispagestyle{empty}
\begin{picture}(50,50)
	\put(17,0){}
	\put(4.5,-13){\footnotesize{دانشگاه صنعتی امیرکبیر}}
	\put(10.5,-27){\footnotesize{(پلی‌تکنیک تهران)}}
	\put(170,30){\bf{به نام خدا}}
	\put(135,-5){\Large\bf{تعهدنامه اصالت اثر}}
	\put(310,0){تاریخ: \datethesis}
\end{picture}

\vspace*{2.5cm}

اينجانب {\bf{\fname\lname}} متعهد می‌شوم که مطالب مندرج در این پایان‌نامه حاصل کار پژوهشی اینجانب تحت نظارت و راهنمایی اساتید دانشگاه صنعتی امیرکبیر بوده و به دستاوردهای دیگران که در این پژوهش از آنها استفاده شده است مطابق مقررات و روال متعارف ارجاع و در فهرست منابع و مآخذ ذکر گردیده است. این پایان‌نامه قبلاً برای احراز هیچ مدرک هم‌سطح یا بالاتر ارائه نگردیده است.

در صورت اثبات تخلف در هر زمان، مدرک تحصیلی صادر شده توسط دانشگاه از درجه اعتبار ساقط بوده و دانشگاه حق پیگیری قانونی خواهد داشت.

کلیه نتایج و حقوق حاصل از این پایان‌نامه متعلق به دانشگاه صنعتی امیرکبیر می‌باشد. هرگونه استفاده از نتایج علمی و عملی، واگذاری اطلاعات به دیگران یا چاپ و تکثیر، نسخه‌برداری، ترجمه و اقتباس از این پایان نامه بدون موافقت کتبی دانشگاه صنعتی امیرکبیر ممنوع است. 
نقل مطالب با ذکر مآخذ بلامانع است.\\
\vspace{2.5cm}

{\centerline {\bf{\fname\lname}}}
\vspace*{.2cm}
{\centerline{امضا}}

	\begin{figure}[!h]
	\centering
	
	\end{figure}
%%%%%%%%%%%%%%%%%%%%%%%%%%%%%%%%%

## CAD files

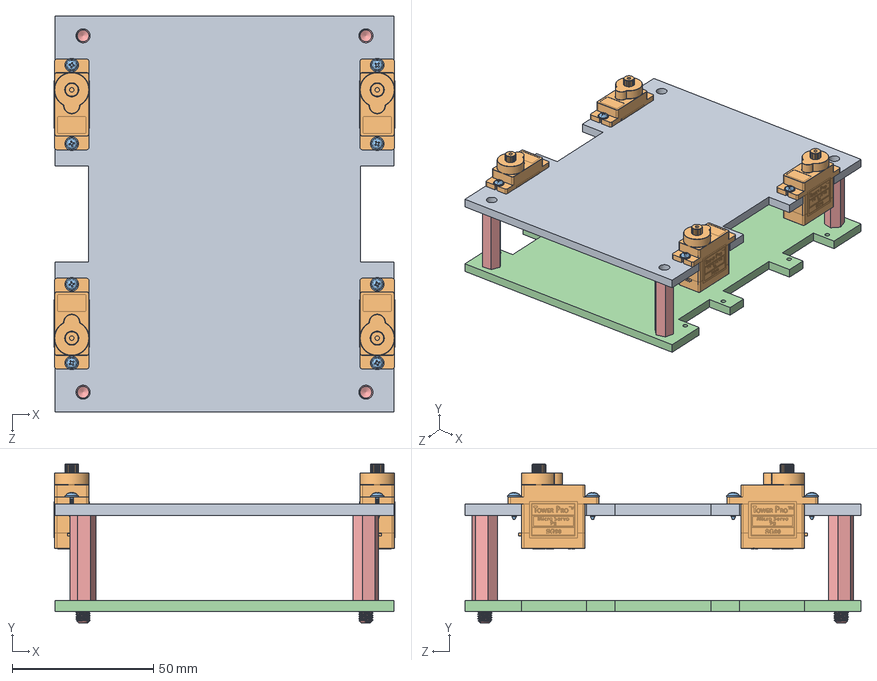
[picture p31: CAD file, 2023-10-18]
Solid/V1(1.05.1401)/Assem1.SLDASM
120.4 x 56.1 x 140.0 mm
Upper_Layer
SG90 - Micro Servo 9g - Tower Pro.1 x 4
SG90 - Micro Servo 9g - Tower Pro.5 x 8
Bottom_Layer
hex standoff spacer_M5_L30.stp x 4

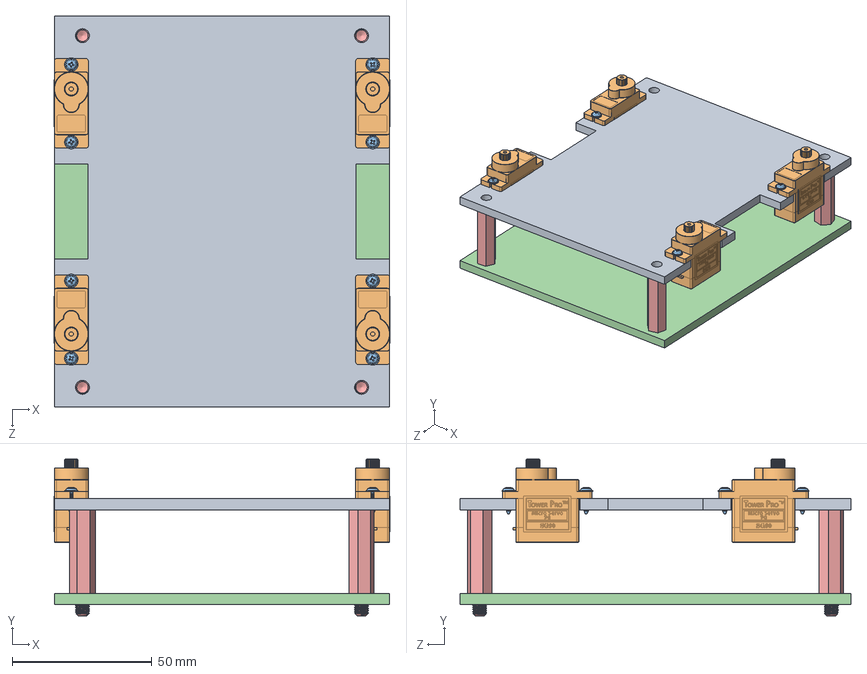
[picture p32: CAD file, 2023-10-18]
Solid/V1(1.05.1401)/Assembly/Assem1.SLDASM
120.4 x 56.1 x 140.0 mm
Upper_Layer
SG90 - Micro Servo 9g - Tower Pro.1 x 4
SG90 - Micro Servo 9g - Tower Pro.5 x 8
Bottom_Layer
hex standoff spacer_M5_L30.stp x 4

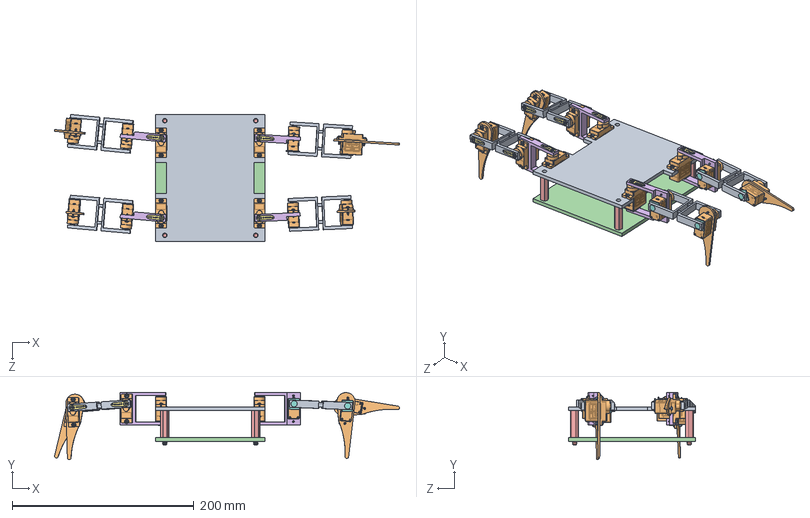
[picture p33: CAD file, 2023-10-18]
Solid/V2(23.05.1401)/Assem1.SLDASM
379.3 x 74.1 x 140.0 mm
Upper_Layer
SG90 - Micro Servo 9g - Tower Pro.1 x 12
SG90 - Micro Servo 9g - Tower Pro.5 x 24
Bottom_Layer
hex standoff spacer_M5_L30.stp x 4
Link_1 x 4
SG90 - Micro Servo 9g - Tower Pro.2 x 12
Shaft_Under_Motor x 12
Link_2 x 4
Link_3 x 4

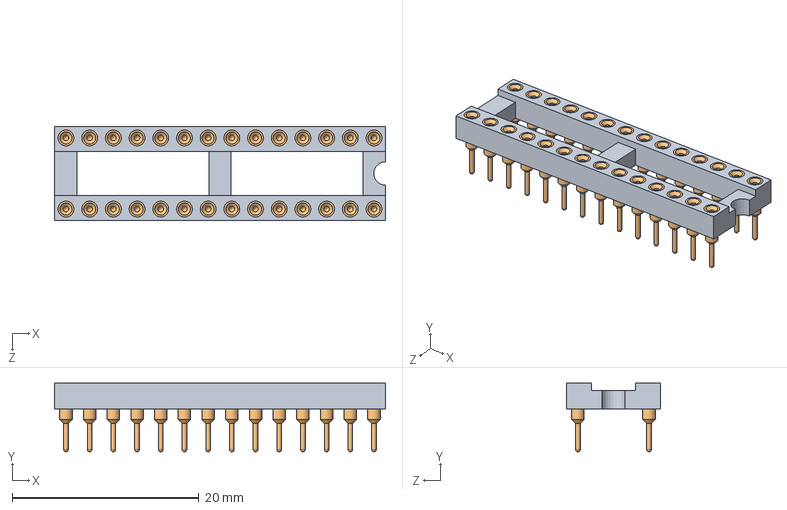
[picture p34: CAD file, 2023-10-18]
Solid/V4(18.02.1402)/arduino uno/dip28.SLDASM
35.5 x 7.37 x 10.1 mm
dip28
dip socket pin x 28

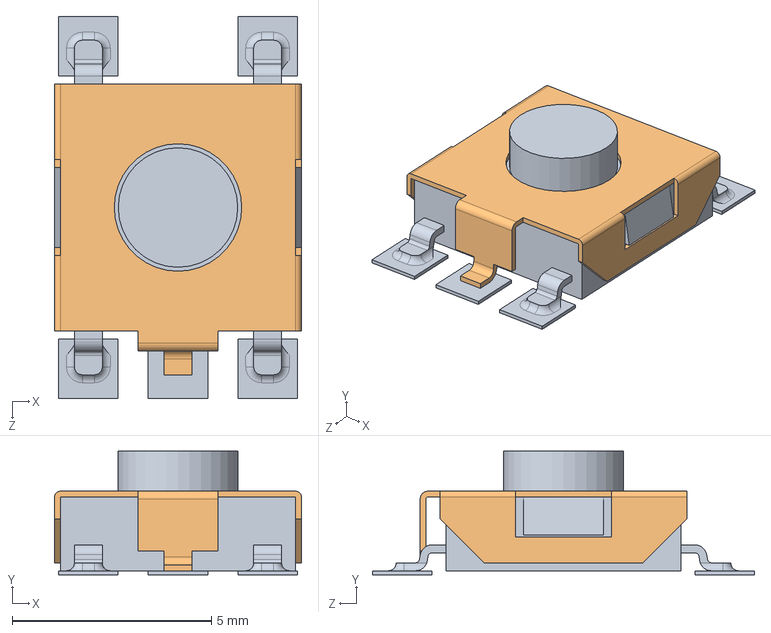
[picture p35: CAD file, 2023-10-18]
Solid/V3(27.01.1402)/arduino uno/RESET BUTTON.SLDASM
6.20 x 3.10 x 9.60 mm
RESET CORE
RESET

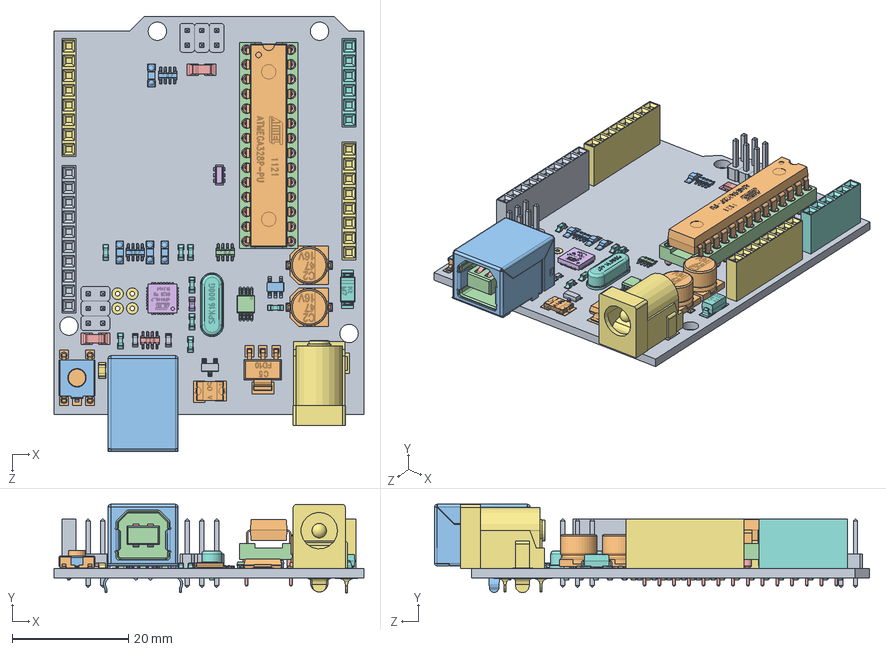
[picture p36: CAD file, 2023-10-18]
Solid/V3(27.01.1402)/arduino uno/arduino uno.SLDASM
53.3 x 15.2 x 74.9 mm
unoboard blue
47uf CAP Dcase x 2
USB SHELL
USB core
usb top contact x 2
usb btm contact x 2
power jack
crystal
2pin_header__02 x 6
nano - reg
led x 4
dip28
dip socket pin x 28
atmega16u2
8 PORT HEADER x 2
6 PORT HEADER
10 PORT HEADER
ATMEL328P
102 RESISTOR PACK x 2
103 RESISTOR PACK
220 RESISTOR PACK
16mhz crystal - measured
PADS001
603 cap on pad x 8
ssot3
mf-msmf050-2
lmv358
lp2985dgkr
cd1206 diode x 2
603 resistor
blm21
m7 diode
MLC0603 x 2
RESET CORE
RESET

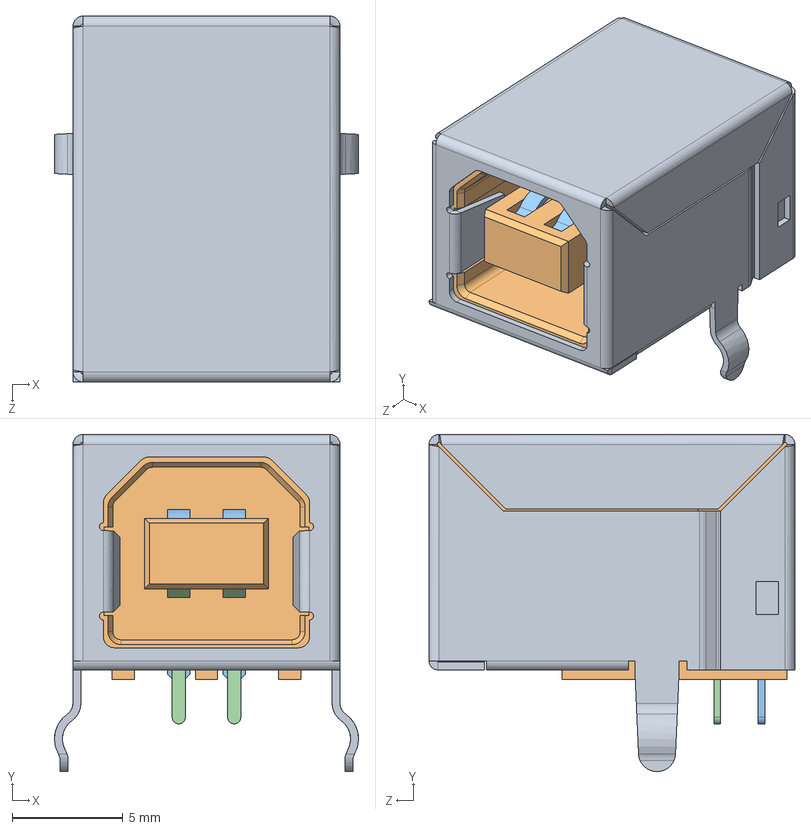
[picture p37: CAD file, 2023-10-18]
Solid/V3(27.01.1402)/arduino uno/USB type b.SLDPRT.SLDASM
13.7 x 15.2 x 16.5 mm
USB SHELL
USB core
usb top contact x 2
usb btm contact x 2

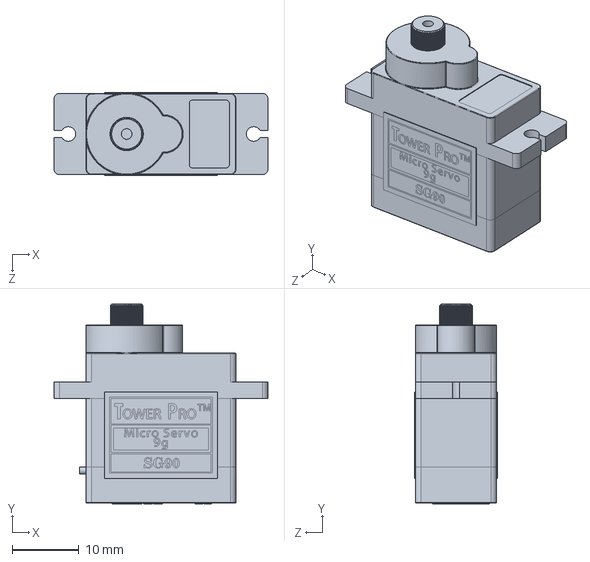
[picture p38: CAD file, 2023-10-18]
Solid/V1(1.05.1401)/Assembly/SG90 - Micro Servo 9g - Tower Pro.1.SLDPRT
32.1 x 30.0 x 12.4 mm

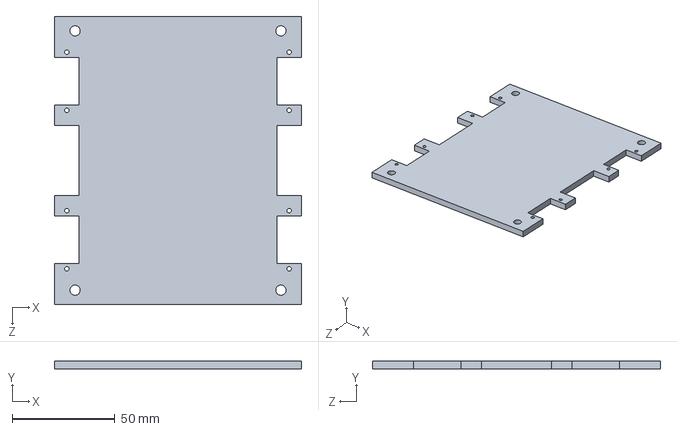
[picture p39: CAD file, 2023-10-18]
Solid/V1(1.05.1401)/Upper_Layer.SLDPRT
120.0 x 4.00 x 140.0 mm

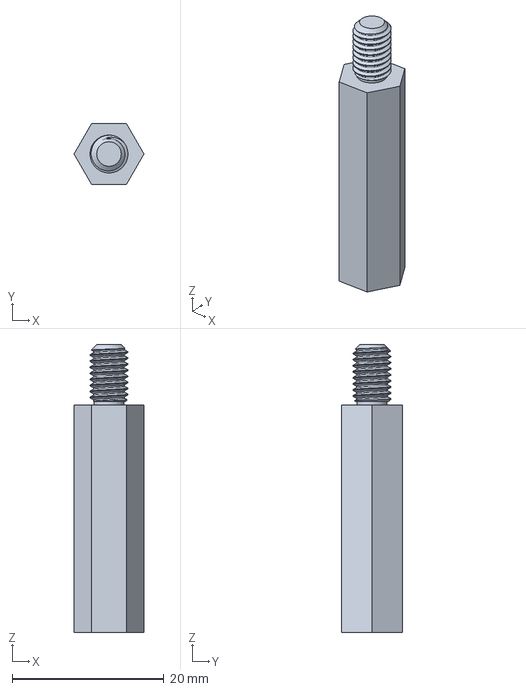
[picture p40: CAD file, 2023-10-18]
Solid/V2(23.05.1401)/hex standoff spacer_M5_L30.stp
9.24 x 8.00 x 38.0 mm

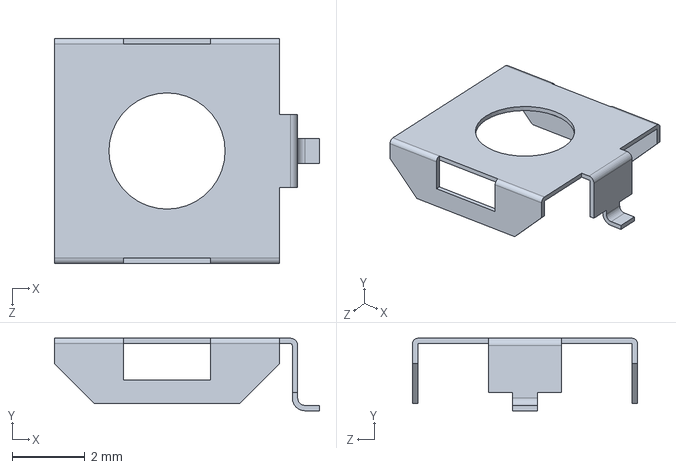
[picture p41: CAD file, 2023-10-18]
Solid/V3(27.01.1402)/arduino uno/RESET.SLDPRT
7.30 x 2.00 x 6.20 mm

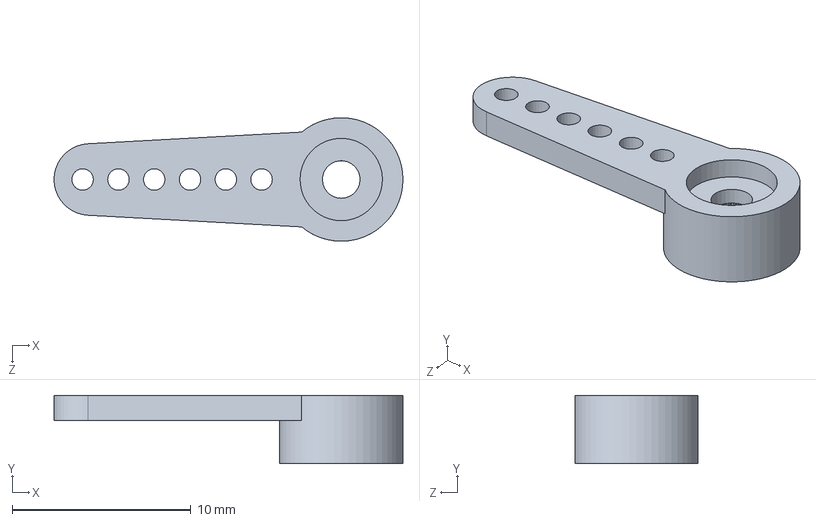
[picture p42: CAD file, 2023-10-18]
Solid/V3(27.01.1402)/SG90 - Micro Servo 9g - Tower Pro.2.SLDPRT
19.5 x 3.80 x 6.90 mm

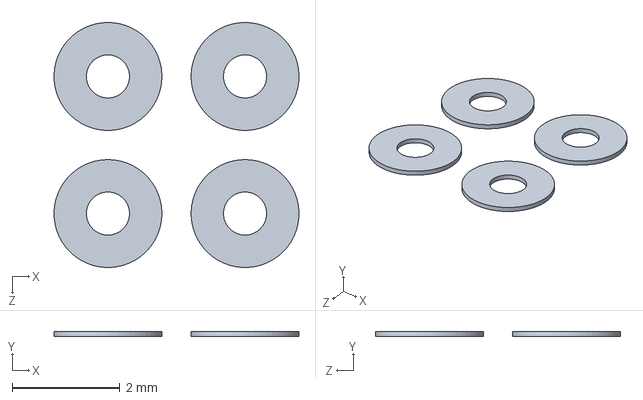
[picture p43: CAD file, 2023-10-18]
Solid/V4(18.02.1402)/arduino uno/PADS001.SLDPRT
4.54 x 0.1 x 4.54 mm

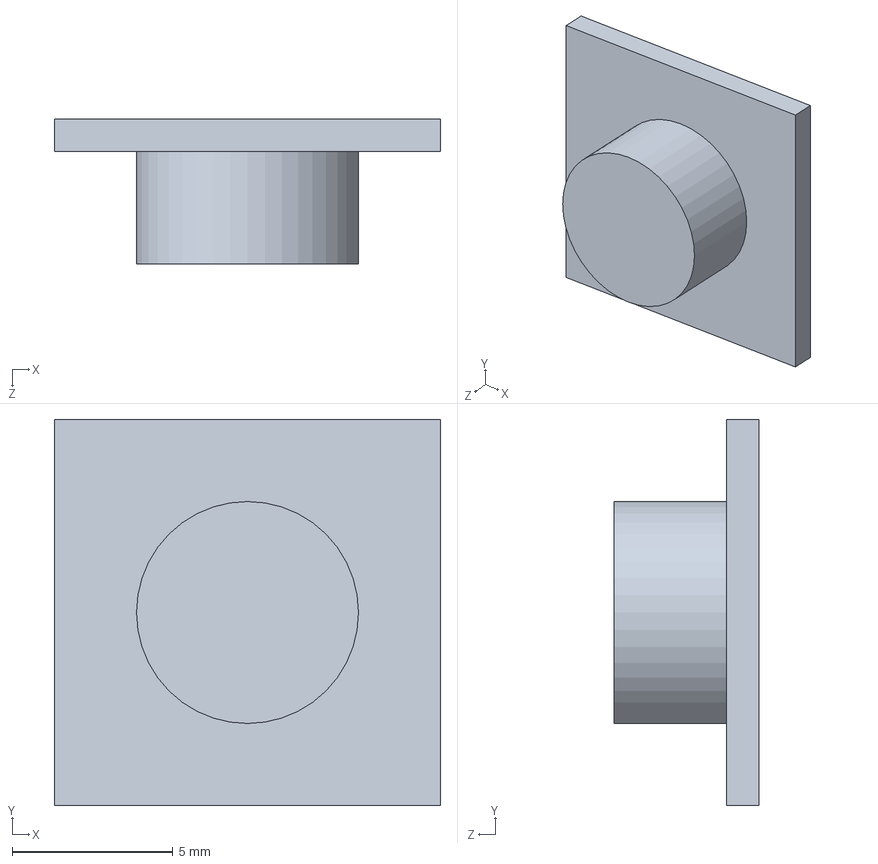
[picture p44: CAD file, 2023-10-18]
Solid/V4(18.02.1402)/Shaft_Under_Motor.SLDPRT
12.0 x 12.0 x 4.50 mm

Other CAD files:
Solid/V1(1.05.1401)/Assembly/Bottom_Layer.SLDPRT
Solid/V1(1.05.1401)/Assembly/SG90 - Micro Servo 9g - Tower Pro.5.SLDPRT
Solid/V1(1.05.1401)/Assembly/Upper_Layer.SLDPRT
Solid/V1(1.05.1401)/SG90 - Micro Servo 9g - Tower Pro.5.SLDPRT
Solid/V2(23.05.1401)/Bottom_Layer.SLDPRT
Solid/V2(23.05.1401)/Link_1.SLDPRT
Solid/V2(23.05.1401)/Link_2.SLDPRT
Solid/V2(23.05.1401)/Link_3.SLDPRT
Solid/V2(23.05.1401)/SG90 - Micro Servo 9g - Tower Pro.5.SLDPRT
Solid/V2(23.05.1401)/Upper_Layer.SLDPRT
Solid/V3(27.01.1402)/Bottom_Layer.SLDPRT
Solid/V3(27.01.1402)/LiPo Battery v5.step
Solid/V3(27.01.1402)/Link_1.SLDPRT
Solid/V3(27.01.1402)/Link_2.SLDPRT
Solid/V3(27.01.1402)/Link_3.SLDPRT
Solid/V3(27.01.1402)/MIni - 360.step
Solid/V3(27.01.1402)/SG90 - Micro Servo 9g - Tower Pro.5.SLDPRT
Solid/V3(27.01.1402)/STL/Bottom_Layer.STL
Solid/V3(27.01.1402)/STL/Upper_Layer.STL
Solid/V3(27.01.1402)/Upper_Layer.SLDPRT
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

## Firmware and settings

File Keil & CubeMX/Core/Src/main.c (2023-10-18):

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
/* Includes ------------------------------------------------------------------*/
#include "main.h"
#include "dma.h"
#include "tim.h"
#include "usart.h"
#include "gpio.h"


/* USER CODE BEGIN PV */
/*Setting an initial value for the angle of each motor.*/
int Motor_Current_Position[4][5] = {{0, 0, 0, 0, 0}, {0, 79, 75, 77, 78}, 
{0, 125, 116, 117, 125}, {0, 94, 86, 90, 85}}; 
int space = 0, count = 0;
char symbol;
uint8_t RxBuffer[4];
/* USER CODE END PV */

void SystemClock_Config(void);
/* USER CODE BEGIN PFP */
int Find_max(int pwm_1, int pwm_2, int pwm_3, int pwm_4);
void Move_All(int pwm_1, int pwm_2, int pwm_3, int pwm_4, int motor);
void Move(TIM_HandleTypeDef htim, int timer, int CCR, int pwm, int motor);
void Home(void);
void Forward(int count);
void Backward(int count);
void Turn_Left(int count);
void Turn_Right(int count);
void deCode(void);
void HAL_UART_RxCpltCallback(UART_HandleTypeDef *huart);
/* USER CODE END PFP */

/* USER CODE BEGIN 0 */
////////////////////////////////////////////////////////////////////////////////////
/* USER CODE END 0 */

/**
  * @brief  The application entry point.
  * @retval int
  */
int main(void)
{
  /* MCU Configuration--------------------------------------------------------*/

  /* Reset of all peripherals, Initializes the Flash interface and the Systick. */
  HAL_Init();

  /* Configure the system clock */
  SystemClock_Config();

  /* Initialize all configured peripherals */
  MX_GPIO_Init();
  MX_DMA_Init();
  MX_USART1_UART_Init();
  MX_TIM1_Init();
  MX_TIM2_Init();
  MX_TIM3_Init();
  MX_TIM4_Init();
  /* USER CODE BEGIN 2 */
	////////////////////////////////////////////////////////////// Leg1
	HAL_TIM_PWM_Start(&htim1, TIM_CHANNEL_1); //A8	=> M3
	HAL_TIM_PWM_Start(&htim3, TIM_CHANNEL_4);	//B1	=> M2
	HAL_TIM_PWM_Start(&htim4, TIM_CHANNEL_4); //B9  => M1
	////////////////////////////////////////////////////////////// Leg2
	HAL_TIM_PWM_Start(&htim2, TIM_CHANNEL_2);	//A1	=> M3
	HAL_TIM_PWM_Start(&htim2, TIM_CHANNEL_3); //A2	=> M2
	HAL_TIM_PWM_Start(&htim2, TIM_CHANNEL_4);	//A3	=> M1
	////////////////////////////////////////////////////////////// Leg3
	HAL_TIM_PWM_Start(&htim3, TIM_CHANNEL_1); //A6	=> M1
	HAL_TIM_PWM_Start(&htim3, TIM_CHANNEL_2);	//A7	=> M2
	HAL_TIM_PWM_Start(&htim3, TIM_CHANNEL_3); //B0	=> M3
	////////////////////////////////////////////////////////////// Leg4
	HAL_TIM_PWM_Start(&htim4, TIM_CHANNEL_1); //B6	=> M1
	HAL_TIM_PWM_Start(&htim4, TIM_CHANNEL_2);	//B7	=> M2
	HAL_TIM_PWM_Start(&htim4, TIM_CHANNEL_3); //B8	=> M3
  /* USER CODE END 2 */

  /* Infinite loop */
  /* USER CODE BEGIN WHILE */
	HAL_UART_Receive_DMA(&huart1, RxBuffer, 4);
	Home();
	
  while (1)
  {
    /* USER CODE END WHILE */

    /* USER CODE BEGIN 3 */
		switch(symbol)
		{
			case 'P':
				if(space < 110)
					Forward(1);
				else
				{
					Turn_Right(5);
					Forward(11);
					Turn_Left(5);
					Forward(11);
					Turn_Right(5);
				}
				break;
			case 'B':
				if(space < 105)
					Forward(1);
				else
					Forward(20);
				break;
		}
  }
  /* USER CODE END 3 */
}

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
/* USER CODE BEGIN 4 */
/*Finding the maximum value among the four motors.*/
int Find_max(int pwm_1, int pwm_2, int pwm_3, int pwm_4)
{
	int max = pwm_1;
	if(max < pwm_2)
		max = pwm_2;
	if(max < pwm_3)
		max = pwm_3;
	if(max < pwm_4)
		max = pwm_4;
	return max;
}
////////////////////////////////////////////////////////////////////////////////
/*Simultaneously moving all four motors in a row.*/
void Move_All(int pwm_1, int pwm_2, int pwm_3, int pwm_4, int motor)
{
	int n, max;
	max = Find_max(pwm_1, pwm_2, pwm_3, pwm_4);
	switch(motor)
	{
		case 1:
			n = 50;
			for(;n <= max;n++)
			{
				if(pwm_3 >= n)
					htim3.Instance->CCR1 = n;
				if(pwm_1 >= n)
					htim4.Instance->CCR4 = n;
				if(pwm_4 >= n)
					htim4.Instance->CCR1 = n;
				if(pwm_2 >= n)
					htim2.Instance->CCR4 = n;
				HAL_Delay(10);
			}
			break;
		case 2:
			n = 70;
			for(;n <= max;n++)
			{
				if(pwm_3 >= n)
					htim3.Instance->CCR2 = n;
				if(pwm_1 >= n)
					htim3.Instance->CCR4 = n;
				if(pwm_4 >= n)
					htim4.Instance->CCR2 = n;
				if(pwm_2 >= n)
					htim2.Instance->CCR3 = n;
				HAL_Delay(10);
			}
			break;
		case 3:
			n = 45;
			for(;n <= max;n++)
			{
				if(pwm_3 >= n)
					htim3.Instance->CCR3 = n;
				if(pwm_1 >= n)
					htim1.Instance->CCR1 = n;
				if(pwm_4 >= n)
					htim4.Instance->CCR3 = n;
				if(pwm_2 >= n)
					htim2.Instance->CCR2 = n;
				HAL_Delay(10);
			}
			break;
	}
}
////////////////////////////////////////////////////////////////////////////////
/*Moving the motor to a desired angle.*/
void Move(TIM_HandleTypeDef htim, int timer, int CCR, int pwm, int motor)
{
	int n;
	if( timer == 3 && CCR == 3)
		n = Motor_Current_Position[motor][1];
	else if( timer == 4 && CCR == 4)
		n = Motor_Current_Position[motor][1];
	else
		n = Motor_Current_Position[motor][timer];
	if(n <= pwm)
	{
		switch(CCR)
		{
			case 1:
					for(;n <= pwm;n++)
					{
						htim.Instance->CCR1 = n;
						HAL_Delay(10);
					}
					break;
			case 2:
					for(;n <= pwm;n++)
					{
						htim.Instance->CCR2 = n;
						HAL_Delay(10);
					}
					break;
			case 3:
					for(;n <= pwm;n++)
					{
						htim.Instance->CCR3 = n;
						HAL_Delay(10);
					}
					break;
			case 4:
					for(;n <= pwm;n++)
					{
						htim.Instance->CCR4 = n;
						HAL_Delay(10);
					}
					break;
		}
	}
	else
	{
		switch(CCR)
		{
			case 1:
					for(;n >= pwm;n--)
					{
						htim.Instance->CCR1 = n;
						HAL_Delay(10);
					}
					break;
			case 2:
					for(;n >= pwm;n--)
					{
						htim.Instance->CCR2 = n;
						HAL_Delay(10);
					}
					break;
			case 3:
					for(;n >= pwm;n--)
					{
						htim.Instance->CCR3 = n;
						HAL_Delay(10);
					}
					break;
			case 4:
					for(;n >= pwm;n--)
					{
						htim.Instance->CCR4 = n;
						HAL_Delay(10);
					}
					break;
		}
	}
	if( timer == 3 && CCR == 3)
		Motor_Current_Position[motor][1] = pwm;
	else if( timer == 4 && CCR == 4)
		Motor_Current_Position[motor][1] = pwm;
	else
		Motor_Current_Position[motor][timer] = pwm;
}
////////////////////////////////////////////////////////////////////////////////
/*Initial state of the robot in complete stability.*/
void Home()
{
	HAL_Delay(2000);
	Move_All(79, 75, 77, 78, 1);
	Move_All(125, 116, 117, 125, 2);
	Move_All(94, 86, 90, 85, 3); 
	HAL_Delay(1000);
}
////////////////////////////////////////////////////////////////////////////////
/*Moving forward by the desired amount.*/
void Forward(int count)
{
	for(int i = 1;i <= count;i++)
	{
		///////////////////////////
		Move(htim3, 3, 2, 107, 2); 
		Move(htim3, 3, 3, 80, 3);  
		Move(htim4, 4, 1, 103, 1);
		Move(htim3, 3, 2, 117, 2); 
		Move(htim3, 3, 3, 90, 3); 
		Move(htim2, 2, 3, 111, 2); 
		Move(htim2, 2, 2, 76, 3);  
		Move(htim4, 4, 1, 78,1);
		Move(htim2, 2, 3, 116, 2); 
		Move(htim2, 2, 2, 86, 3); 
		HAL_Delay(300);
		///////////////////////////  
		Move(htim2, 2, 3, 106, 2);
		Move(htim2, 2, 2, 76, 3);
		Move(htim4, 4, 4, 54, 1); 	
		Move(htim2, 2, 3, 116, 2);
		Move(htim2, 2, 2, 86, 3);
		Move(htim3, 3, 2, 112, 2); 
		Move(htim3, 3, 3, 85, 3);
		Move(htim4, 4, 4, 79, 1);
		Move(htim3, 3, 2, 117, 2); 
		Move(htim3, 3, 3, 90, 3);
		HAL_Delay(300);
	}
}
////////////////////////////////////////////////////////////////////////////////
/*Moving backward by the desired amount.*/
void Backward(int count)
{
	for(int i = 1;i <= count;i++)
	{
		///////////////////////////
		Move(htim4, 4, 2, 115, 2); 
		Move(htim4, 4, 3, 75, 3);  
		Move(htim3, 3, 1, 102, 1);
		Move(htim4, 4, 2, 125, 2); 
		Move(htim4, 4, 3, 85, 3); 
		Move(htim3, 3, 4, 120, 2); 
		Move(htim1, 1, 1, 89, 3);  
		Move(htim3, 3, 1, 77,1);
		Move(htim3, 3, 4, 125, 2); 
		Move(htim1, 1, 1, 94, 3); 
		HAL_Delay(300);
		///////////////////////////  
		Move(htim3, 3, 4, 115, 2);
		Move(htim1, 1, 1, 84, 3);
		Move(htim2, 2, 4, 50, 1); 	
		Move(htim3, 3, 4, 125, 2);
		Move(htim1, 1, 1, 94, 3);
		Move(htim4, 4, 2, 120, 2); 
		Move(htim4, 4, 3, 80, 3);
		Move(htim2, 2, 4, 75, 1);
		Move(htim4, 3, 2, 125, 2); 
		Move(htim4, 3, 3, 85, 3);
		HAL_Delay(300);
	}
}
////////////////////////////////////////////////////////////////////////////////
/*Turning left by the desired amount.*/
void Turn_Left(int count)
{
	Move(htim2, 2, 3, 111, 2);
	for(int i = 1;i <= count;i++)
	{
		///////////////////////////
		Move(htim4, 4, 2, 110, 2); 
		Move(htim4, 4, 3, 70, 3);  
		Move(htim3, 3, 1, 107, 1);
		Move(htim4, 4, 2, 125, 2); 
		Move(htim4, 4, 3, 85, 3); 
		///////////////////////////
		Move(htim3, 3, 3, 70, 3);
		Move(htim4, 4, 1, 108, 1);
		Move(htim3, 3, 3, 90, 3);
		for(int p = 1;p <= 30;p++)
		{
			htim3.Instance->CCR1 = 107 - p;
			htim4.Instance->CCR1 = 108 - p;
			HAL_Delay(10);
		}
		Motor_Current_Position[1][3] = 77;
		Motor_Current_Position[1][4] = 78;
		HAL_Delay(300);
	}
	Move(htim2, 2, 3, 116, 2);
}
////////////////////////////////////////////////////////////////////////////////
/*Turning right by the desired amount.*/
void Turn_Right(int count)
{
	Move(htim3, 3, 2, 114, 2);
	for(int i = 1;i <= count;i++)
	{
		///////////////////////////
		Move(htim2, 2, 3, 101, 2); 
		Move(htim2, 2, 2, 71, 3);  
		Move(htim4, 4, 4, 49, 1);
		Move(htim2, 2, 3, 116, 2); 
		Move(htim2, 2, 2, 86, 3); 
		///////////////////////////
		Move(htim1, 1, 1, 74, 3);
		Move(htim2, 2, 4, 45, 1);
		Move(htim1, 1, 1, 94, 3);
		for(int p = 1;p <= 30;p++)
		{
			htim4.Instance->CCR4 = 49 + p;
			htim2.Instance->CCR4 = 45 + p;
			HAL_Delay(10);
		}
		Motor_Current_Position[1][1] = 79;
		Motor_Current_Position[1][2] = 75;
		HAL_Delay(300);
	}
	Move(htim3, 3, 2, 117, 2);
}
////////////////////////////////////////////////////////////////////////////////
void deCode()
{
	int index = 5;
	if(RxBuffer[0] == 66 || RxBuffer[0] == 78 || RxBuffer[0] == 80 || RxBuffer[0] == 89) 
	{
		index = 0;
		symbol = RxBuffer[0];
	}
	else if(RxBuffer[1] == 66 || RxBuffer[1] == 78 || RxBuffer[1] == 80 || RxBuffer[1] == 89) 
	{
		index = 1;
		symbol = RxBuffer[1];
	}
	else if(RxBuffer[2] == 66 || RxBuffer[2] == 78 || RxBuffer[2] == 80 || RxBuffer[2] == 89) 
	{
		index = 2;
		symbol = RxBuffer[2];
	}
	else if(RxBuffer[3] == 66 || RxBuffer[3] == 78 || RxBuffer[3] == 80 || RxBuffer[3] == 89)
	{
		index = 3;
		symbol = RxBuffer[3];
	}
	switch(index)
	{
		case 0:
			space = (RxBuffer[3] - 48) + (RxBuffer[2] - 48) * 10 + (RxBuffer[1] - 48) * 100;
			break;
		case 1:
			space = (RxBuffer[0] - 48) + (RxBuffer[3] - 48) * 10 + (RxBuffer[2] - 48) * 100;
			break;
		case 2:
			space = (RxBuffer[1] - 48) + (RxBuffer[0] - 48) * 10 + (RxBuffer[3] - 48) * 100;
			break;
		case 3:
			space = (RxBuffer[2] - 48) + (RxBuffer[1] - 48) * 10 + (RxBuffer[0] - 48) * 100;
			break;
	}
}
////////////////////////////////////////////////////////////////////////////////
void HAL_UART_RxCpltCallback(UART_HandleTypeDef *huart)
{
	if(huart == &huart1){
		deCode();
	}
}
/* USER CODE END 4 */
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


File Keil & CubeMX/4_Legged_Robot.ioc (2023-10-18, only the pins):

Mcu.UserName=STM32F103C8Tx
PA1.Signal=S_TIM2_CH2
PA10.Signal=USART1_RX
PA13.Signal=SYS_JTMS-SWDIO
PA14.Signal=SYS_JTCK-SWCLK
PA2.Signal=S_TIM2_CH3
PA3.Signal=S_TIM2_CH4
PA6.Signal=S_TIM3_CH1
PA7.Signal=S_TIM3_CH2
PA8.Signal=S_TIM1_CH1
PA9.Signal=USART1_TX
PB0.Signal=S_TIM3_CH3
PB1.Signal=S_TIM3_CH4
PB6.Signal=S_TIM4_CH1
PB7.Signal=S_TIM4_CH2
PB8.Signal=S_TIM4_CH3
PB9.Signal=S_TIM4_CH4
PD0-OSC_IN.Signal=RCC_OSC_IN
PD1-OSC_OUT.Signal=RCC_OSC_OUT

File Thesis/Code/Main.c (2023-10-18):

switch(Which color detected?)
{
  if(The obstacle is Pink) 
    if(The area of the obstacle has exceeded the limit or not?)
      Forward(1);
    else
    {
       Turn_Right(5);
       Forward(11);
       Turn_Left(5);
       Forward(11);
       Turn_Right(5);
    }
  if(The obstacle is Blue)
    if(The area of the obstacle has exceeded the limit or not?)
      Forward(1);
    else
      Forward(20);
}

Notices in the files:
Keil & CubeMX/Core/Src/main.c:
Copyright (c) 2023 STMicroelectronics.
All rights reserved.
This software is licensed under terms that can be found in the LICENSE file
